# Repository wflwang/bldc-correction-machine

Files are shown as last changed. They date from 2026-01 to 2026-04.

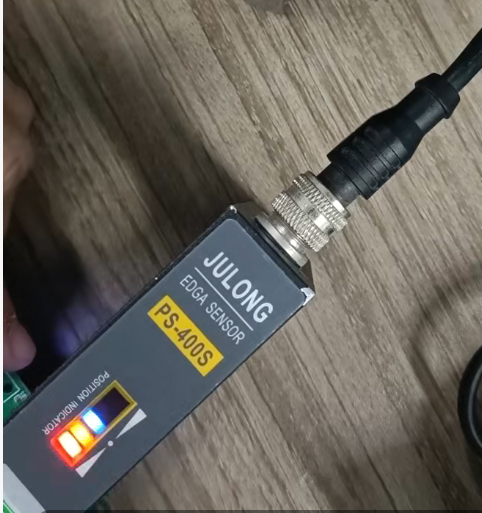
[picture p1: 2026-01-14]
纠偏机方案(1)/纠偏机方案/4602f8ad32d056c3740c5eb95091c43c.png

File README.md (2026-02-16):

# BLDC纠编机

## 脚位说明
CIU32F003x5 QFN20:
18,19,20  PA5,PA6,PA7 TIM3_CH1,CH3,CH2 用于Hall输入
1 PC0 -> SWDIO
2 PC1 -> TIM1_CH1 3 PB7 -> TIM1_CH1N
4 VSS
5 PB6 AD_6  U
6 VDD
7 PB5 -> TIM1_CH3N 
8 PB4 -> Dir
9 PB3 -> AD_5 V
10 PB2 -> TIM1_CH3
11 PB1 -> TIM1_CH2N
12 PB0 -> TIM1_CH2
13 PA0 -> GetPWM
14 PA1 -> En
15 PA2 -> SWCLK
16 PA3 -> AD_1 W
17 PA4 -> AD_2 VDD

## 使用说明
MDK 工程文件可以编译

drive_paramters.h  马达参数配置
deadErr: 设置死区大小
PID 可以调节速度环和位置环 和PID调整间隔
targets.h  IO 和一些功能配置
可以选择 GyroEn 开启陀螺仪 否则直接固定位置 方便调PID分离陀螺仪干扰影响

串口115200 可以调参

MCU/HK32G003/Inc/peripherals.h 可以看可以调哪些参数
### 自动学习
在新的结构或第一次下载程序时候 需要自动学习,没有学习过的云台没有功能
学习错误的云台功能错乱
##### 学习步骤
1. 开机前云台需要水平放在水平的桌面上,开口朝上
2. 长按 L M R 三个按键3s开机,识别到云台水平朝上放置时候会开机并进入自动学习模式
3. 绿灯快速闪烁svpwm慢慢逐个输出不同角度 一直到经历8个极对,实际7极对(主要学习霍尔最大最小值)
4. 通过旋转一圈求出最大最小值换算出霍尔的中点值,继续旋转
绿灯慢闪 表示进入下一步矫正
5. 把云台垂直放置在桌面上,按键朝上,短按按键绿灯快闪进入第二步学习
6. 绿灯快速闪烁检测陀螺仪是否处于静止,静止时候矫正陀螺仪和加速度
##### 修改学习步骤
1. 7极对电机需要学习7组数据 xy max min 需要对应不同极对里
记录每个极对x范围和y范围 后面查询的时候直接定位到根据x查询到哪个极对范围 再用y最后筛选
换算出不同的 x_offset y_offset x_Amp y_Amp(求出xy 增益的比例,不同)

### 关于

flash 32个word 256byte 一个 page 共 64 个page 第1&2个page 作为bootloader  最后2个page作为EEPROM(存储磁编每一个角度值(256byte*2) 和上次陀螺仪的校准值)
中间 60个page 作为flash 程序空间

## 历史

## 版本

## 邮箱
* [email](https://B5106D@Outlook.com)

## 仓库
* [Gitee](https://gitee.com/wflwang/bldc-correction-machine.git)
* [Github](https://github.com/wflwang/bldc-.git)

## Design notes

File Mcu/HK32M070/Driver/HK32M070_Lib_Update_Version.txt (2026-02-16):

/*
* @file name: HK32M070_Lib_Update_Version
* @description: 本文件是用来描述HK32M070系列芯片函数库版本列表
* @author: AE Team
*/

V1.0.2/2025-12-24
1、删除PGA_CALCLK相关函数和寄存器；

V1.0.1/2025-02-21
1、更新GPIO寄存器；2、删除ADC 拓展寄存器（ADC_ADEF）LPF相关函数。

V1.0.0/2025-02-18
1. 首次发布

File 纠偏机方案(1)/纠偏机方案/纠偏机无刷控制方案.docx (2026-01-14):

在方向端给一个PWM波，做到100HZ赫兹的频率甚至更噶还能保证电机方向能迅速切换

在使用时电机动作幅度很小，可能就转几十度甚至更小，但是需要来回的在正反转之间切换，

精度要求不高，转的角度是根据传感器来的，每次都不一样 然后对低速的扭矩有一定要求

配备自适应/模糊PID算法闭环！驱动功率要求大一点，电流做到10A-20A

驱动芯片需要带霍尔位置反馈，并断电记忆

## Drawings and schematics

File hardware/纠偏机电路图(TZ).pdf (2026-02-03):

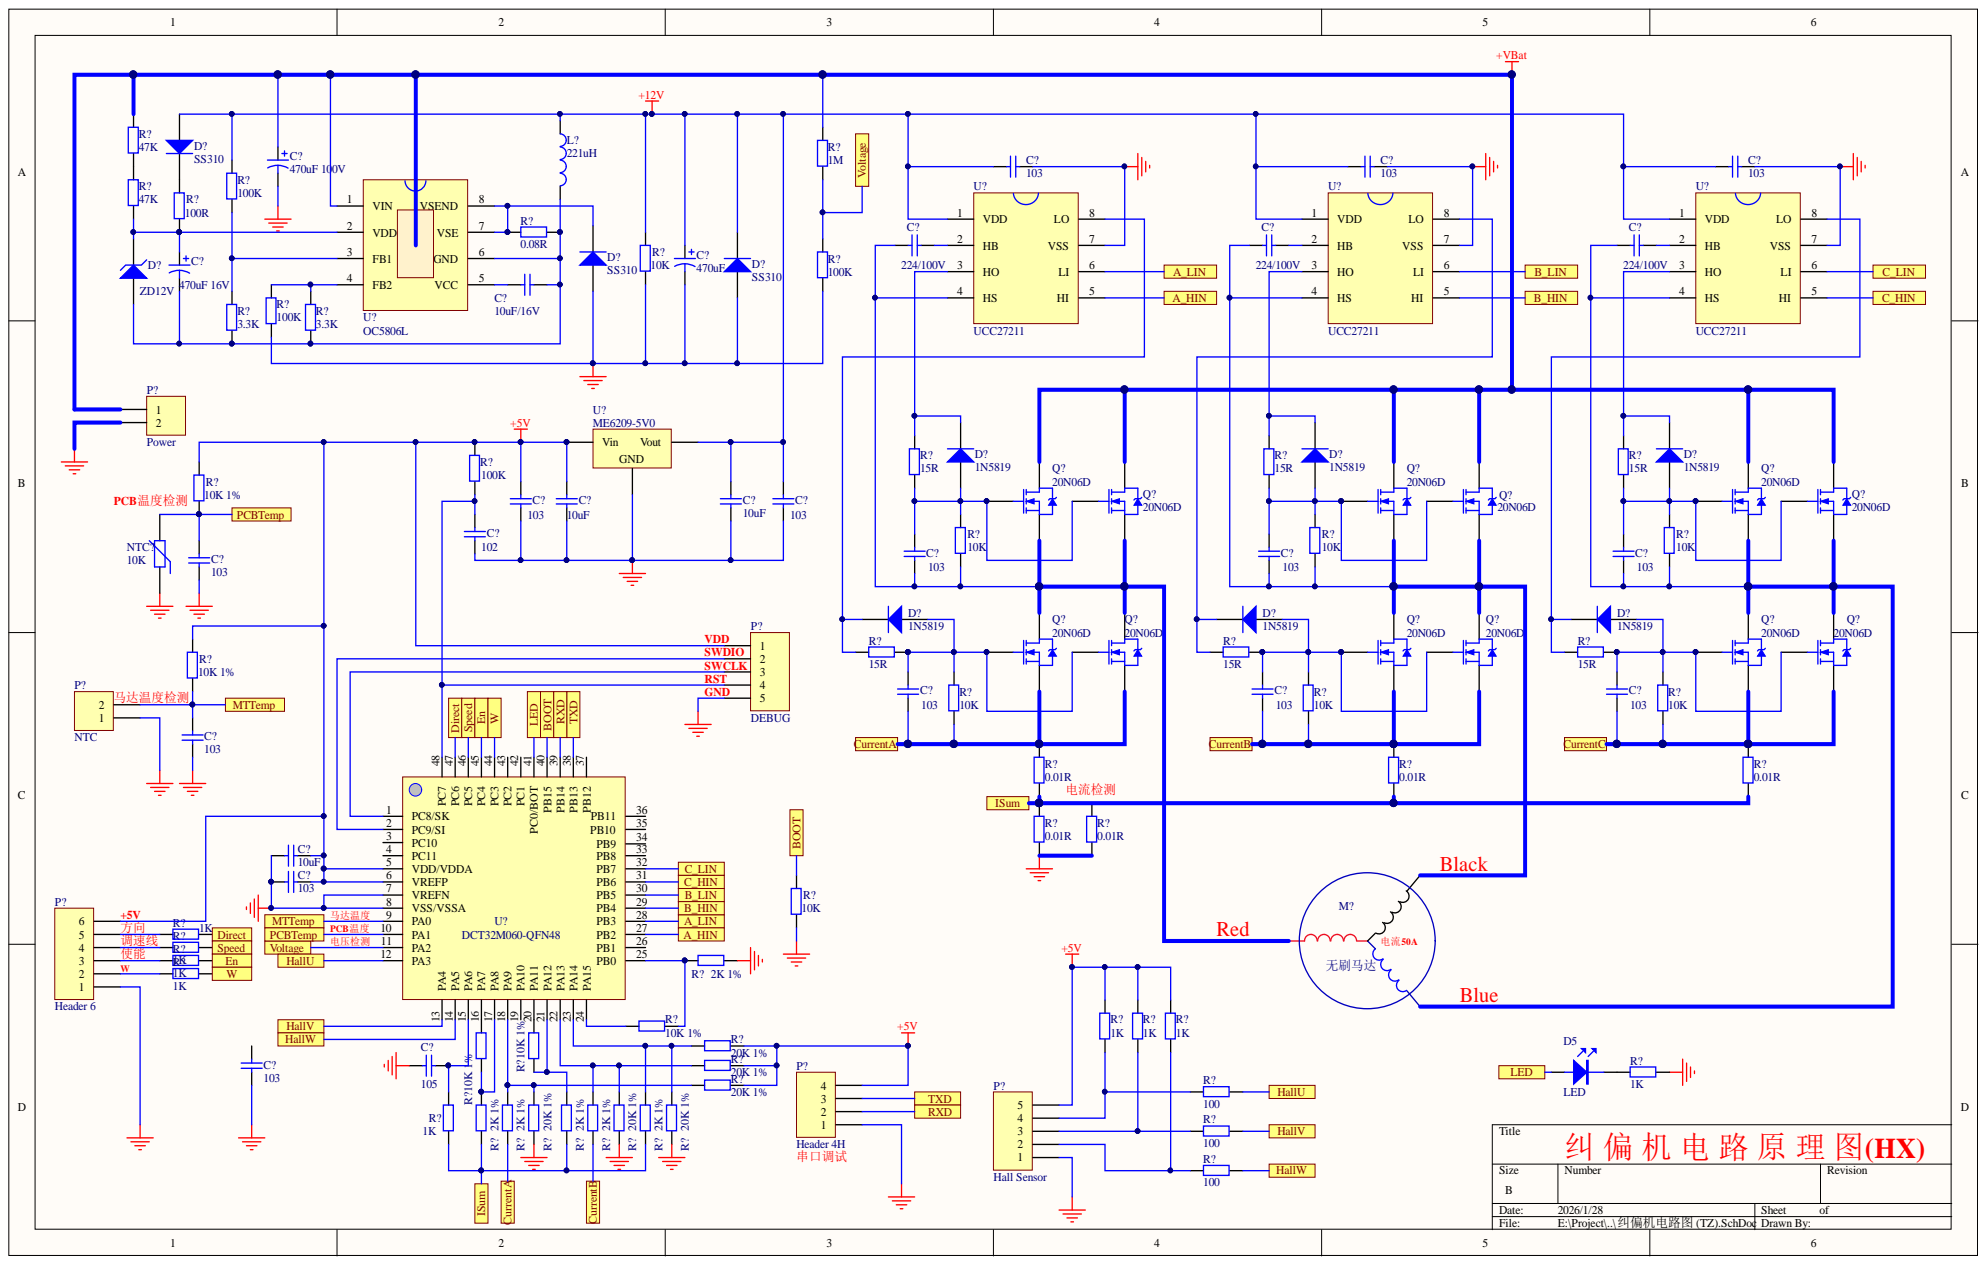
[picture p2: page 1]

SWDIO
SWCLK
RST

PC8/SK 1 | 36 B12 37 PB13 38 PB14 39 PB15 40 PC0/BOT 41 PC1 42 PC2 43 PC3 44 PC4 45 PC5 46 PC6 47 PC7 48

10uF | | VDD/VDDA 5 | 25 PB1 26 PB2 27 PB3 28 PB4 29 PB5 30 PB6 31 PB7 32 PB8 33 PB9 34 PB10

PC10 3 | PB0 U? DCT32M060-QFN48 | 35 PB11 P
PC9/SI 2

ISum

Red | Black

1K R? | | PCB温度 | PA1 10

MTTemp | | | | A_LIN

调速线 | R? | | Direct | | PCBTemp | 电压检测 | PA2 11 | A_HIN
使能 | R? | | Speed | | Voltage | | PA3 12

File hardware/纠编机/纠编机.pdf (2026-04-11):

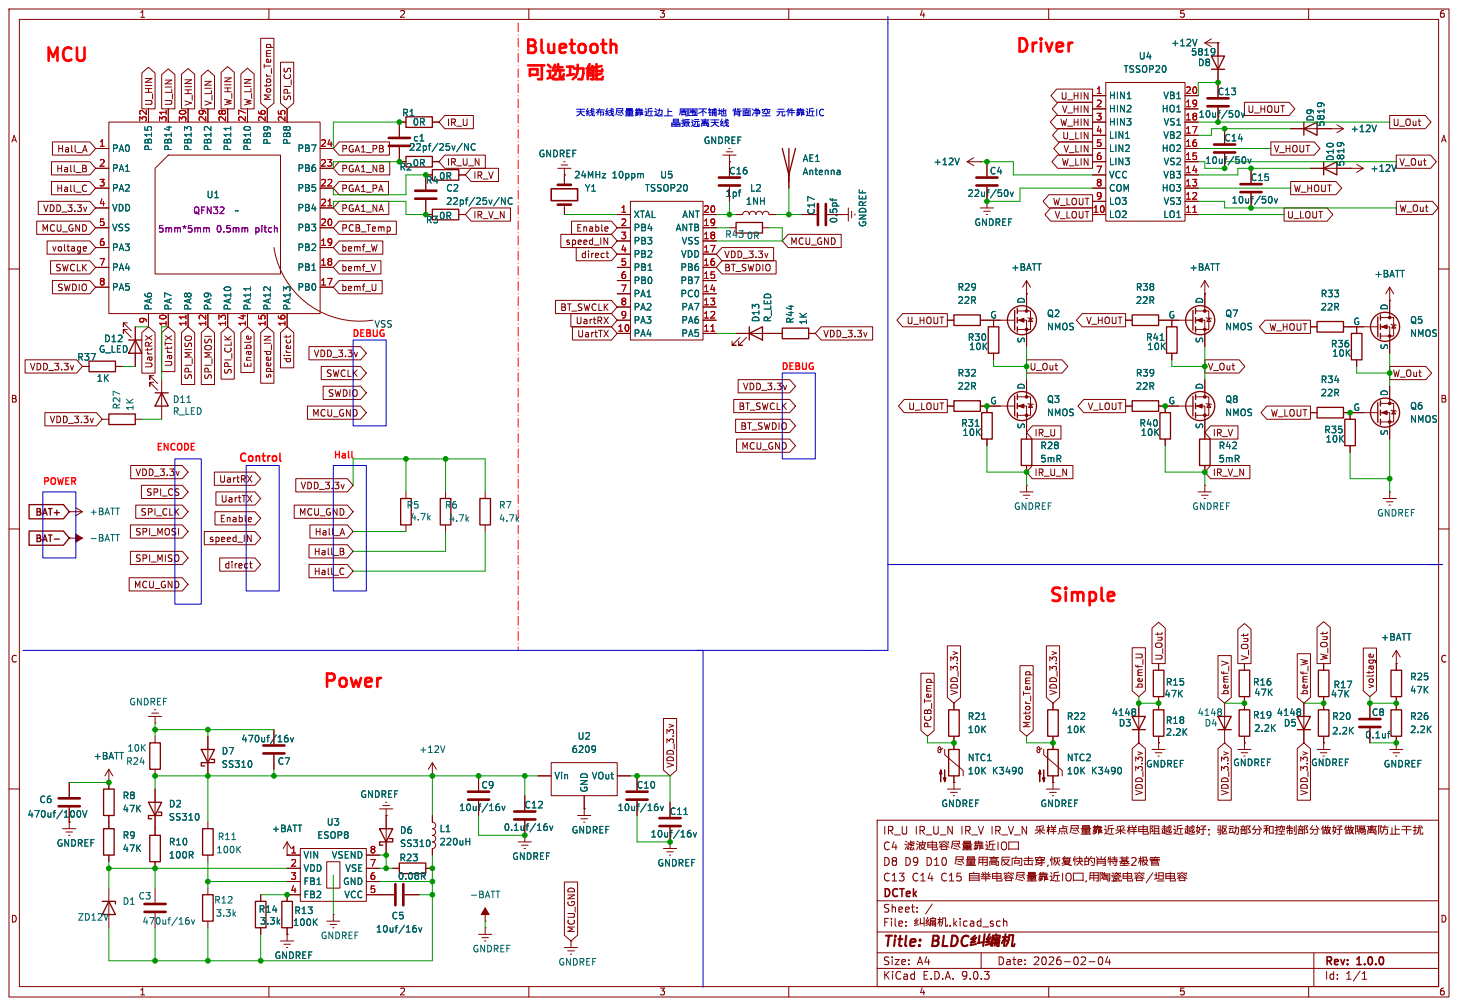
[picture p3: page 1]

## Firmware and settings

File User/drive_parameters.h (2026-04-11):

/**
  ******************************************************************************
  * @file    drive_parameters.h
  * @version V1.0.0
  * @brief   This file contains the parameters for MOTOR controler.
  ******************************************************************************
  */

/* Define to prevent recursive inclusion -------------------------------------*/
#ifndef __DRIVE_PARAMETERS_H
#define __DRIVE_PARAMETERS_H

/************************
 *** Motor Parameters ***
 ************************/
#ifndef SQRT_3
#define SQRT_3  1.732
#endif

/************************* CPU & ADC PERIPHERAL CLOCK CONFIG ******************/
#define SYSCLK_FREQ                          64000000uL
#define TIM_CLOCK_DIVIDER                    1
#define ADV_TIM_CLK_MHz                      64
#define ADC_CLK_MHz                          16uL /* Maximum ADC Clock Frequency expressed in MHz */
#define HALL_TIM_CLK                         64000000uL
#define ADC_REFERENCE_VOLTAGE                5
/***************** MOTOR ELECTRICAL PARAMETERS  ******hDTCompCnt************************/
#define POLE_PAIR_NUM                        40 //4       /*!< Number of motor pole pairs */
#define RS                                   3.2     /*!< Stator resistance, ohm */
#define LS                                   0.00043 /*!< Stator inductance, H For I-PMSM it is equal to Lq */
#define LdS                                   0.00023 /*!< Stator inductance, H For I-PMSM it is equal to Lq */
#define LqS                                   0.00023 /*!< Stator inductance, H For I-PMSM it is equal to Lq */
#define FluxLink                             3.232 //磁链


#define Q12RLF(x) (x*0x1fffffff)
/* When using Id = 0, NOMINAL_CURRENT is utilized to saturate the output of the
   PID for speed regulation (i.e. reference torque).
   Transformation of real currents (A) into int16_t format must be done accordingly with
   formula:
   Phase current (int16_t 0-to-peak) = (Phase current (A 0-to-peak)* 32767 * Rshunt *
                                   *Amplifying network gain)/(MCU supply voltage/2)
*/
#define NOMINAL_CURRENT                      2100
#define MOTOR_MAX_SPEED_RPM                  4000 /*!< Maximum rated speed  */
#define MOTOR_VOLTAGE_CONSTANT               2.45 /*!< Volts RMS ph-ph /kRPM */


/***************** MOTOR SENSORS PARAMETERS  ******************************/
/* Motor sensors parameters are always generated but really meaningful only
   if the corresponding sensor is actually present in the motor         */

/*** Hall sensors ***/
#define HALL_SENSORS_PLACEMENT               DEGREES_120   /*!< Define here the mechanical position of the sensors withreference to an electrical cycle.It can be either DEGREES_120 or DEGREES_60 */
#define HALL_PHASE_SHIFT                     120           /*!< Define here in degrees the electrical phase shift between the low to high transition of signal H1 and the maximum of the Bemf induced on phase A */

/*********** Bus voltage sensing section ****************/
#define VBUS_PARTITIONING_FACTOR             0.091         /*!< It expresses how much the Vbus is attenuated before being converted into digital value */
#define NOMINAL_BUS_VOLTAGE_V                24

/******** Current reading parameters section ******/
/*** Topology ***/
#define THREE_SHUNT
#define RSHUNT                               0.005

/*  ICSs gains in case of isolated current sensors, amplification gain for shunts based sensing */
#define OPA_GAIN     PGA1_PGA_GAIN_12
#define AMPLIFICATION_GAIN                   12.0 //3.2//5.18 
//#define AMPLIFICATION_GAIN_IBUS              3.2

/*** Noise parameters ***/
#define TNOISE_NS                            1000
#define TRISE_NS                             1000

/************ Temperature sensing section ***************/
/* V[V]=V0+dV/dT[V/Celsius]*(T-T0)[Celsius]*/
#define V0_V                                 1.055   /*!< in Volts */
#define T0_C                                 25      /*!< in Celsius degrees */
#define dV_dT                                0.023   /*!< V/Celsius degrees */
#define T_MAX                                110     /*!< Sensor measured temperature at maximum power stage working temperature, Celsius degrees */

/******** MAIN AND AUXILIARY SPEED/POSITION SENSOR(S) SETTINGS SECTION ********/

/*** Speed measurement settings ***/
#define MAX_APPLICATION_SPEED                4000 /*!< rpm, mechanical */
#define MIN_APPLICATION_SPEED                0    /*!< rpm, mechanical, absolute value */
#define MEAS_ERRORS_BEFORE_FAULTS            3    /*!< Number of speed  
                                                       measurement errors before 
                                                       main sensor goes in fault */

/****** Hall sensors ************/
#define HALL_MEAS_ERRORS_BEFORE_FAULTS       3 /*!< Number of failed   
                                                    derived class specific speed 
                                                    measurements before main sensor  
                                                    goes in fault */
                                             
#define HALL_AVERAGING_FIFO_DEPTH            16 /*!< depth of the FIFO used to 
                                                     average mechanical speed in 
                                                     0.1Hz resolution */
                                                           
/**************************    DRIVE SETTINGS SECTION   **********************/
/* PWM generation and current reading */
#define PWM_FREQUENCY                        12000
                                             
#define LOW_SIDE_SIGNALS_ENABLING            LS_PWM_TIMER
#define SW_DEADTIME_NS                       700 /*!< Dead-time to be inserted  
                                                       by FW, only if low side 
                                                       signals are enabled */
/* Torque and flux regulation loops */
#define REGULATION_EXECUTION_RATE            1  /*!< FOC execution rate in number of PWM cycles */

/* Gains values for torque and flux control loops */
#define PID_TORQUE_KP_DEFAULT                300   //1204
#define PID_TORQUE_KI_DEFAULT                600   //242
                                             
#define PID_FLUX_KP_DEFAULT                  250   //1804
#define PID_FLUX_KI_DEFAULT                  520   //542
//弱磁时候开d轴弱磁PI控制 达到最高转速的85%的时候切换到更高的id PI
#define PID_FLUX_KP_H                  470   //1804
#define PID_FLUX_KI_H                  1000  //542

/* Torque/Flux control loop gains dividers*/
#define TF_KPDIV                             16384
#define TF_KIDIV                             16384
#define TF_KDDIV                             16384

/* Speed control loop */
#define SPEED_LOOP_FREQUENCY_HZ              1000   /*!< Execution rate of speed regulation loop (Hz) */
#define PID_SPEED_KP_DEFAULT                 620
#define PID_SPEED_KI_DEFAULT                 3800
#define PID_SPEED_KD_DEFAULT                 0
//高速时候切换到高速PID                                             
#define PID_HSPEED_KP_DEFAULT                 400
#define PID_HSPEED_KI_DEFAULT                 3800
#define PID_HSPEED_KD_DEFAULT                 0
/* Speed PID parameter dividers */           
#define SP_KPDIV                             128
#define SP_KIDIV                             16384
#define SP_KDDIV                             8192

/* Default settings */
#define DEFAULT_CONTROL_MODE                 STC_SPEED_MODE /*!< STC_TORQUE_MODE or STC_SPEED_MODE */
#define DEFAULT_TARGET_SPEED_RPM             1000
#define DEFAULT_TORQUE_COMPONENT             0  //4266
#define DEFAULT_FLUX_COMPONENT               0

/**************************    FIRMWARE PROTECTIONS SECTION   *****************/
#define OV_VOLTAGE_PROT_ENABLING             ENABLE
#define UV_VOLTAGE_PROT_ENABLING             ENABLE
#define OV_VOLTAGE_THRESHOLD_V               50   /*!< Over-voltage threshold */
#define UD_VOLTAGE_THRESHOLD_V               8    /*!< Under-voltage threshold */
#define R_BRAKE_SWITCH_OFF_THRES_V           
#define OV_TEMPERATURE_THRESHOLD_C           110  /*!< Celsius degrees */
#define OV_TEMPERATURE_HYSTERESIS_C          10   /*!< Celsius degrees */

/*  Feed-forward parameters */
/*  Maximum Torque Per Ampere strategy parameters */
#define IQMAX                                32767 //15594

#endif /*__DRIVE_PARAMETERS_H*/

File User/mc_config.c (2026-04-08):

/**
  ******************************************************************************
  * @file    mc_config.c
  * @version V1.0.0
  * @date    2021-07-30
  ******************************************************************************
  */

#include "main.h"
#include "mc_type.h"
#include "parameters_conversion.h"
#include "mc_parameters.h"
#include "mc_config.h"
#include "hw_correct.h"
#include "app.h"
#include "mc_tasks.h"

#define MAX_TWAIT 0                 /* Dummy value for single drive */
#define FREQ_RATIO 1                /* Dummy value for single drive */
#define FREQ_RELATION HIGHEST_FREQ  /* Dummy value for single drive */

#define OFFCALIBRWAIT_MS     0
#define OFFCALIBRWAIT_MS2    0

extern int16_t foc_hall_ang_table[8];


//mc_config_t mcconf;     //初始化 马达配置
//app_config_t appconf;   //app config
//#include "pqd_motor_power_measurement.h"

//PQD_MotorPowMeas_Handle_t PQD_MotorPowMeasM1 =
//{
//    .wConvFact = PQD_CONVERSION_FACTOR
//};
//PQD_MotorPowMeas_Handle_t *pPQD_MotorPowMeasM1 = &PQD_MotorPowMeasM1;

/**
  * @brief  PI / PID Speed loop parameters Motor 1
  */
PID_Handle_t PIDSpeedHandle_M1 =
{
    .hDefKpGain          = (int16_t)PID_SPEED_KP_DEFAULT,
    .hDefKiGain          = (int16_t)PID_SPEED_KI_DEFAULT,
    .hDefKdGain          = (int16_t)PID_SPEED_KD_DEFAULT,
    .wUpperIntegralLimit = (int32_t)IQMAX * (int32_t)SP_KIDIV,
    .wLowerIntegralLimit = -(int32_t)IQMAX * (int32_t)SP_KIDIV,
    .hUpperOutputLimit   = (int16_t)IQMAX,
    .hLowerOutputLimit   = -(int16_t)IQMAX,
    .hKpDivisor          = (uint16_t)SP_KPDIV,
    .hKiDivisor          = (uint16_t)SP_KIDIV,
    .hKpDivisorPOW2      = (uint16_t)SP_KPDIV_LOG,
    .hKiDivisorPOW2      = (uint16_t)SP_KIDIV_LOG,
    .hKdDivisor          = (uint16_t)SP_KDDIV_LOG,
    .hKdDivisorPOW2      = (uint16_t)SP_KDDIV_LOG,
    .hCompensation      = 0,
};

/**
  * @brief  PI / PID Iq loop parameters Motor 1
  */
PID_Handle_t PIDIqHandle_M1 =
{
    .hDefKpGain          = (int16_t)PID_TORQUE_KP_DEFAULT,
    .hDefKiGain          = (int16_t)PID_TORQUE_KI_DEFAULT,
    .wUpperIntegralLimit = (int32_t)INT16_MAX * TF_KIDIV,
    .wLowerIntegralLimit = (int32_t) - INT16_MAX * TF_KIDIV,
    .hUpperOutputLimit   = INT16_MAX,
    .hLowerOutputLimit   = -INT16_MAX,
    .hKpDivisor          = (uint16_t)TF_KPDIV,
    .hKiDivisor          = (uint16_t)TF_KIDIV,
    .hKpDivisorPOW2      = (uint16_t)TF_KPDIV_LOG,
    .hKiDivisorPOW2      = (uint16_t)TF_KIDIV_LOG,
    .hDefKdGain          = 0x0000U,
    .hKdDivisor          = 0x0000U,
    .hKdDivisorPOW2      = 0x0000U,
    .hCompensation      = 0,
};

/**
  * @brief  PI / PID Id loop parameters Motor 1
  */
PID_Handle_t PIDIdHandle_M1 =
{
    .hDefKpGain          = (int16_t)PID_FLUX_KP_DEFAULT,
    .hDefKiGain          = (int16_t)PID_FLUX_KI_DEFAULT,
    .wUpperIntegralLimit = (int32_t)INT16_MAX * TF_KIDIV,
    .wLowerIntegralLimit = (int32_t) - INT16_MAX * TF_KIDIV,
    .hUpperOutputLimit   = INT16_MAX,
    .hLowerOutputLimit   = -INT16_MAX,
    .hKpDivisor          = (uint16_t)TF_KPDIV,
    .hKiDivisor          = (uint16_t)TF_KIDIV,
    .hKpDivisorPOW2      = (uint16_t)TF_KPDIV_LOG,
    .hKiDivisorPOW2      = (uint16_t)TF_KIDIV_LOG,
    .hDefKdGain          = 0x0000U,
    .hKdDivisor          = 0x0000U,
    .hKdDivisorPOW2      = 0x0000U,
    .hCompensation      = 0,
};

/**
  * @brief  SpeednTorque Controller parameters Motor 1
  */
SpeednTorqCtrl_Handle_t SpeednTorqCtrlM1 =
{
    .STCFrequencyHz             =  MEDIUM_FREQUENCY_TASK_RATE,
    .MaxAppPositiveMecSpeed01Hz = (uint16_t)(MAX_APPLICATION_SPEED / 6),
    .MinAppPositiveMecSpeed01Hz = (uint16_t)(MIN_APPLICATION_SPEED / 6),
    .MaxAppNegativeMecSpeed01Hz = (int16_t)(-MIN_APPLICATION_SPEED / 6),
    .MinAppNegativeMecSpeed01Hz = (int16_t)(-MAX_APPLICATION_SPEED / 6),
    .MaxPositiveTorque          = (int16_t)NOMINAL_CURRENT,
    .MinNegativeTorque          = -(int16_t)NOMINAL_CURRENT,
    .ModeDefault                = DEFAULT_CONTROL_MODE,
    .MecSpeedRef01HzDefault     = (int16_t)(DEFAULT_TARGET_SPEED_RPM / 6),
    .TorqueRefDefault           = (int16_t)DEFAULT_TORQUE_COMPONENT,
    .IdrefDefault               = (int16_t)DEFAULT_FLUX_COMPONENT,
};
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

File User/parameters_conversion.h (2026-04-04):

/**
  ******************************************************************************
  * @file    parameters_conversion.h
  * @author  Motor Control SDK Team, ST Microelectronics
  * @brief   This file includes the proper Parameter conversion on the base
  *          of stdlib for the first drive
  ******************************************************************************
  */

/* Define to prevent recursive inclusion -------------------------------------*/
#ifndef __PARAMETERS_CONVERSION_H
#define __PARAMETERS_CONVERSION_H
#include "parameters_conversion_f0xx.h"
#include "mc_math.h"


/************************* CONTROL FREQUENCIES & DELAIES **********************/
#define TF_REGULATION_RATE             (uint16_t) ((uint16_t)(PWM_FREQUENCY)/REGULATION_EXECUTION_RATE)
#define REP_COUNTER                    (uint16_t) ((REGULATION_EXECUTION_RATE *2u)-1u)

#define MEDIUM_FREQUENCY_TASK_RATE     (uint16_t)SPEED_LOOP_FREQUENCY_HZ

#define INRUSH_CURRLIMIT_DELAY_COUNTS  (uint16_t)(INRUSH_CURRLIMIT_DELAY_MS * \
                                       ((uint16_t)SPEED_LOOP_FREQUENCY_HZ)/1000u -1u)

#define SYS_TICK_FREQUENCY             2000

#define MF_TASK_OCCURENCE_TICKS        (SYS_TICK_FREQUENCY/SPEED_LOOP_FREQUENCY_HZ)-1u

/**************************   VOLTAGE CONVERSIONS  ****************************/
#define BUS_ADC_CONV_RATIO             VBUS_PARTITIONING_FACTOR

#define OVERVOLTAGE_THRESHOLD_d        (uint16_t)(OV_VOLTAGE_THRESHOLD_V*65535/\
                                       (ADC_REFERENCE_VOLTAGE/VBUS_PARTITIONING_FACTOR))
#define UNDERVOLTAGE_THRESHOLD_d       (uint16_t)((UD_VOLTAGE_THRESHOLD_V*65535)/\
                                       ((uint16_t)(ADC_REFERENCE_VOLTAGE/\
                                       BUS_ADC_CONV_RATIO)))
#define INT_SUPPLY_VOLTAGE             (uint16_t)(65536/ADC_REFERENCE_VOLTAGE)
                                       
#define DELTA_TEMP_THRESHOLD           (OV_TEMPERATURE_THRESHOLD_C- T0_C)
#define DELTA_V_THRESHOLD              (dV_dT * DELTA_TEMP_THRESHOLD)
#define OV_TEMPERATURE_THRESHOLD_d     ((V0_V + DELTA_V_THRESHOLD)*INT_SUPPLY_VOLTAGE)

#define DELTA_TEMP_HYSTERESIS          (OV_TEMPERATURE_HYSTERESIS_C)
#define DELTA_V_HYSTERESIS             (dV_dT * DELTA_TEMP_HYSTERESIS)
#define OV_TEMPERATURE_HYSTERESIS_d    (DELTA_V_HYSTERESIS*INT_SUPPLY_VOLTAGE)

/*************** Timer for PWM generation & currenst sensing parameters  ******/
#define PWM_PERIOD_CYCLES              (uint16_t)(ADV_TIM_CLK_MHz*\
                                       (unsigned long long)1000000u/((uint16_t)(PWM_FREQUENCY)))

#define DEADTIME_NS                    SW_DEADTIME_NS

#define DEAD_TIME_ADV_TIM_CLK_MHz      (ADV_TIM_CLK_MHz * TIM_CLOCK_DIVIDER)
#define DEAD_TIME_COUNTS_1             (DEAD_TIME_ADV_TIM_CLK_MHz * DEADTIME_NS/1000uL)

#if (DEAD_TIME_COUNTS_1 <= 255)
    #define DEAD_TIME_COUNTS (uint16_t) DEAD_TIME_COUNTS_1
#elif (DEAD_TIME_COUNTS_1 <= 508)
    #define DEAD_TIME_COUNTS (uint16_t)(((DEAD_TIME_ADV_TIM_CLK_MHz * DEADTIME_NS/2) /1000uL) + 128)
#elif (DEAD_TIME_COUNTS_1 <= 1008)
    #define DEAD_TIME_COUNTS (uint16_t)(((DEAD_TIME_ADV_TIM_CLK_MHz * DEADTIME_NS/8) /1000uL) + 320)
#elif (DEAD_TIME_COUNTS_1 <= 2015)
    #define DEAD_TIME_COUNTS (uint16_t)(((DEAD_TIME_ADV_TIM_CLK_MHz * DEADTIME_NS/16) /1000uL) + 384)
#else
    #define DEAD_TIME_COUNTS 510
#endif

#define DTCOMPCNT                      (uint16_t)((DEADTIME_NS * ADV_TIM_CLK_MHz) / 2000)
#define TON_NS                         500
#define TOFF_NS                        500
#define TON                            (uint16_t)((TON_NS * ADV_TIM_CLK_MHz)  / 2000)
#define TOFF                           (uint16_t)((TOFF_NS * ADV_TIM_CLK_MHz) / 2000)
                                       
#define MAX_TNTR_NS                    TRISE_NS

#define SAMPLING_TIME                  (uint16_t)(((uint16_t)(SAMPLING_TIME_NS) * ADV_TIM_CLK_MHz)/1000uL)
#define TRISE                          (uint16_t)((((uint16_t)(TRISE_NS)) * ADV_TIM_CLK_MHz)/1000uL)

#if (TRISE_NS > SAMPLING_TIME_NS)
    #define MAX_TRTS (2 * TRISE)
#else
    #define MAX_TRTS (2 * SAMPLING_TIME)
#endif

#define MAX_TNTR_NS                    TRISE_NS

#define TW_AFTER                       ((uint16_t)(((DEADTIME_NS+MAX_TNTR_NS)*ADV_TIM_CLK_MHz)/1000ul))

/*************** PI divisor  ***************/
#define SP_KPDIV_LOG LOG2(SP_KPDIV)
#define SP_KIDIV_LOG LOG2(SP_KIDIV)
#define SP_KDDIV_LOG LOG2(SP_KDDIV)
#define TF_KPDIV_LOG LOG2(TF_KPDIV)
#define TF_KIDIV_LOG LOG2(TF_KIDIV)
#define TF_KDDIV_LOG LOG2(TF_KDDIV)

/* USER CODE BEGIN virtual temperature */
#define M1_TEMP_SW_FILTER_BW_FACTOR    250u

/* USER CODE END virtual temperature */


#define PQD_CONVERSION_FACTOR          (int32_t)(( 1000 * 3 * ADC_REFERENCE_VOLTAGE ) /\
                                       ( 1.732 * RSHUNT * AMPLIFICATION_GAIN ))


/*** Temporary bridge between workbench data model****/
#define PWM_TIM1                       ATU
#define HALL_TIM2                      HTU
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

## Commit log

2026-01-14 init 纠编机要求
2026-02-03 add schDoc config
    [纠偏机电路图(TZ).SchDoc, 纠编机.kicad_pcb, 纠编机.kicad_sch]
2026-02-06 完善原理图的绘制
    [纠编机.kicad_sch]
2026-02-16 添加vesc的马达驱动框架
2026-02-19 霍尔程序注释添加 准备按照vesc风格霍尔程序写入 但是观测器还需要float优化为Q15
2026-02-22 增加霍尔学习的一些内容
2026-02-23 加一点hall数据角度判断
2026-02-28 增加FOC里面的一些朱姐
2026-03-09 准备把070的驱动部分加入进来 先不管无感观测器 只用霍尔看能否正常运行,后续再加入无感部分
2026-03-10 增加peripherals 的驱动配置 等待正确完善
2026-03-25 新增hw conf 文件
2026-03-26 按照vesc风格改动 但可能寄存器配置不对 会导致很多问题
2026-03-26 这个版本直接按照HK的demo改 把霍尔哪里操作优化一下算了 可以考虑用HK的无感一起.后面再改vesc的 vesc的工作量太大 和HK寄存器移植有很多不同,问题可能会更多
    [mc_config.c, mc_parameters.c]
2026-03-28 用hk的基础上用自己的方式做hall角度插值处理
2026-03-29 修改hall中的一点内容
2026-03-30 新增中断细节修改
2026-03-31 把int整理了下 hk的中断开始加入hall的角度处理
2026-04-02 FOC 扩展内切圆 过调制电压增速
2026-04-03 EEPROM 程序部分完成 扭矩和速度环部分完成 hall自动学习部分待完成
2026-04-04 hall 学习动作完成 接下来还是调整中断和hall 角度处理的完善 以及hall速度的检测滤波 方便速度换反馈
2026-04-08 全部程序基本写好 现在新建keil工程用来编译程序
2026-04-09 新工程编译错误消除
2026-04-10 程序已经可以开环转起来,后续还需要完善闭环程序
2026-04-11 开环程序动起来基本可以 但是hall输出波形不对 实测HALL 需要电压高才比较稳定 但是hall信号不完整 不对称
    [纠编机.kicad_sch]
